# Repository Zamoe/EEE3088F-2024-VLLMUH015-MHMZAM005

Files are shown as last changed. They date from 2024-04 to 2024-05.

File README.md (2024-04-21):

# EEE3088F-2024-VLLMUH015-MHMZAM005 - Group 29
Git Repo for EEE3088F group 29 2024 at the University of Cape Town.

The project for EEE3088F aims to design subassemblies for a micromouse, namely the power and sensing subsystem. 
The GitHub repo contains the Kicad Project files for the final PCBs for the project.

The power system is done by Muhammed Vally - VLLMUH015
The sensing subsystem is done by Zameer Mahomed - MHMZAM005

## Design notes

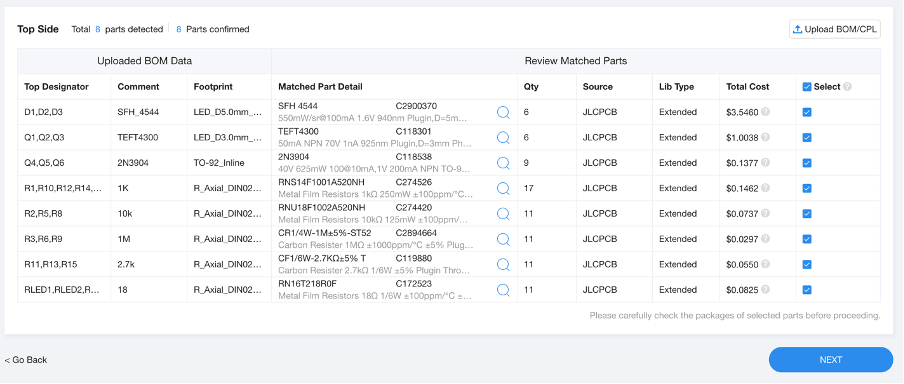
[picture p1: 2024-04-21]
EEE3088F_MHMZAM005_Sensing/jlcpcb/EEE3088F_Project_JLCPCBBOM_MHMZAM005.png

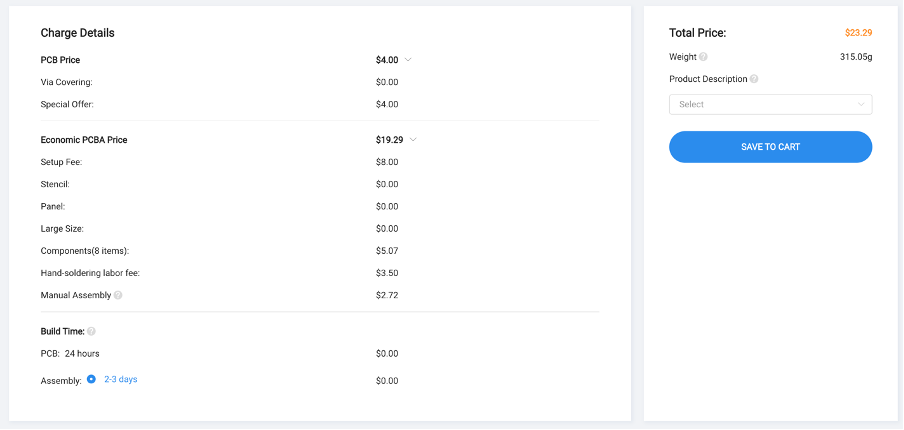
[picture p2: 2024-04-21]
EEE3088F_MHMZAM005_Sensing/jlcpcb/EEE3088F_Project_JLCPCBacceptance_MHMZAM005.png

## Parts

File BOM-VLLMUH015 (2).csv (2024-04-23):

Comment | Designator | Footprint | LCSC
0.1u | C6 | C_0805_2012Metric
10k | R2 | R_0805_2012Metric
0.1u | C5 | C_0805_2012Metric
0.1u | C3 | C_0805_2012Metric
Jumper_2_Open | JP5 | SolderJumper-2_P1.3mm_Bridged2Bar_Pad1.0x1.5mm
1.1k | R4 | R_0805_2012Metric
Jumper_2_Open | JP4 | SolderJumper-2_P1.3mm_Bridged2Bar_Pad1.0x1.5mm
2.2k | R3 | R_0805_2012Metric
10k | R1 | R_0805_2012Metric
Conn_02x01 | J2 | PinSocket_1x02_P2.54mm_Vertical
Jumper_2_Open | JP7 | SolderJumper-2_P1.3mm_Bridged2Bar_Pad1.0x1.5mm
Jumper_2_Open | JP2 | SolderJumper-2_P1.3mm_Bridged2Bar_Pad1.0x1.5mm
Jumper_2_Open | JP1 | SolderJumper-2_P1.3mm_Bridged2Bar_Pad1.0x1.5mm
0.1u | C4 | C_0805_2012Metric
Conn_02x08_Odd_Even | J1 | PinSocket_2x08_P2.54mm_Vertical
DRV8837 | U2 | WSON-8-1EP_2x2mm_P0.5mm_EP0.9x1.6mm
LED | D1 | LED_0805_2012Metric
Jumper_2_Open | JP6 | SolderJumper-2_P1.3mm_Bridged2Bar_Pad1.0x1.5mm
DRV8837 | U3 | WSON-8-1EP_2x2mm_P0.5mm_EP0.9x1.6mm
LED | D2 | LED_0805_2012Metric
10u | C8 | C_0805_2012Metric
0.4 | R6 | R_0805_2012Metric
Conn_01x02_Pin | J3 | PinHeader_1x02_P2.54mm_Vertical
TP4056 | U4 | ESOP8_UMW-L
10u | C7 | C_0805_2012Metric
1k | R7 | R_0805_2012Metric
1k | R8 | R_0805_2012Metric

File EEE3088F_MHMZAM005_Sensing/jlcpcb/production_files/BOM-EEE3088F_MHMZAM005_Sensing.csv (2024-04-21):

Comment | Designator | Footprint | LCSC
TEFT4300 | Q1,Q2,Q3 | LED_D3.0mm_Horizontal_O1.27mm_Z2.0mm | C118301
2N3904 | Q4,Q5,Q6 | TO-92_Inline | C118538
2.7k | R11,R13,R15 | R_Axial_DIN0207_L6.3mm_D2.5mm_P2.54mm_Vertical | C119880
18 | RLED1,RLED2,RLED3 | R_Axial_DIN0207_L6.3mm_D2.5mm_P2.54mm_Vertical | C172523
10k | R2,R5,R8 | R_Axial_DIN0207_L6.3mm_D2.5mm_P2.54mm_Vertical | C274420
1K | R1,R10,R12,R14,R4,R7 | R_Axial_DIN0207_L6.3mm_D2.5mm_P2.54mm_Vertical | C274526
1M | R3,R6,R9 | R_Axial_DIN0207_L6.3mm_D2.5mm_P2.54mm_Vertical | C2894664
SFH_4544 | D1,D2,D3 | LED_D5.0mm_Horizontal_O1.27mm_Z9.0mm | C2900370
Jumper_2_Open | JP4 | SolderJumper-2_P1.3mm_Open_Pad1.0x1.5mm
Jumper_2_Open | JP1 | SolderJumper-2_P1.3mm_Open_Pad1.0x1.5mm
Jumper_2_Open | JP15 | SolderJumper-2_P1.3mm_Open_Pad1.0x1.5mm
Jumper_2_Open | JP13 | SolderJumper-2_P1.3mm_Open_Pad1.0x1.5mm
Jumper_2_Open | JP2 | SolderJumper-2_P1.3mm_Open_Pad1.0x1.5mm
Jumper_2_Open | JP7 | SolderJumper-2_P1.3mm_Open_Pad1.0x1.5mm
Jumper_2_Open | JP5 | SolderJumper-2_P1.3mm_Open_Pad1.0x1.5mm
Jumper_2_Open | JP11 | SolderJumper-2_P1.3mm_Open_Pad1.0x1.5mm
Jumper_2_Open | JP9 | SolderJumper-2_P1.3mm_Open_Pad1.0x1.5mm
Jumper_2_Open | JP6 | SolderJumper-2_P1.3mm_Open_Pad1.0x1.5mm
Jumper_2_Open | JP10 | SolderJumper-2_P1.3mm_Open_Pad1.0x1.5mm
Jumper_2_Open | JP14 | SolderJumper-2_P1.3mm_Open_Pad1.0x1.5mm
Jumper_2_Open | JP3 | SolderJumper-2_P1.3mm_Open_Pad1.0x1.5mm
Jumper_2_Open | JP12 | SolderJumper-2_P1.3mm_Open_Pad1.0x1.5mm
Jumper_2_Open | JP8 | SolderJumper-2_P1.3mm_Open_Pad1.0x1.5mm
Conn_02x14_Odd_Even | J1 | PinHeader_2x14_P2.54mm_Vertical

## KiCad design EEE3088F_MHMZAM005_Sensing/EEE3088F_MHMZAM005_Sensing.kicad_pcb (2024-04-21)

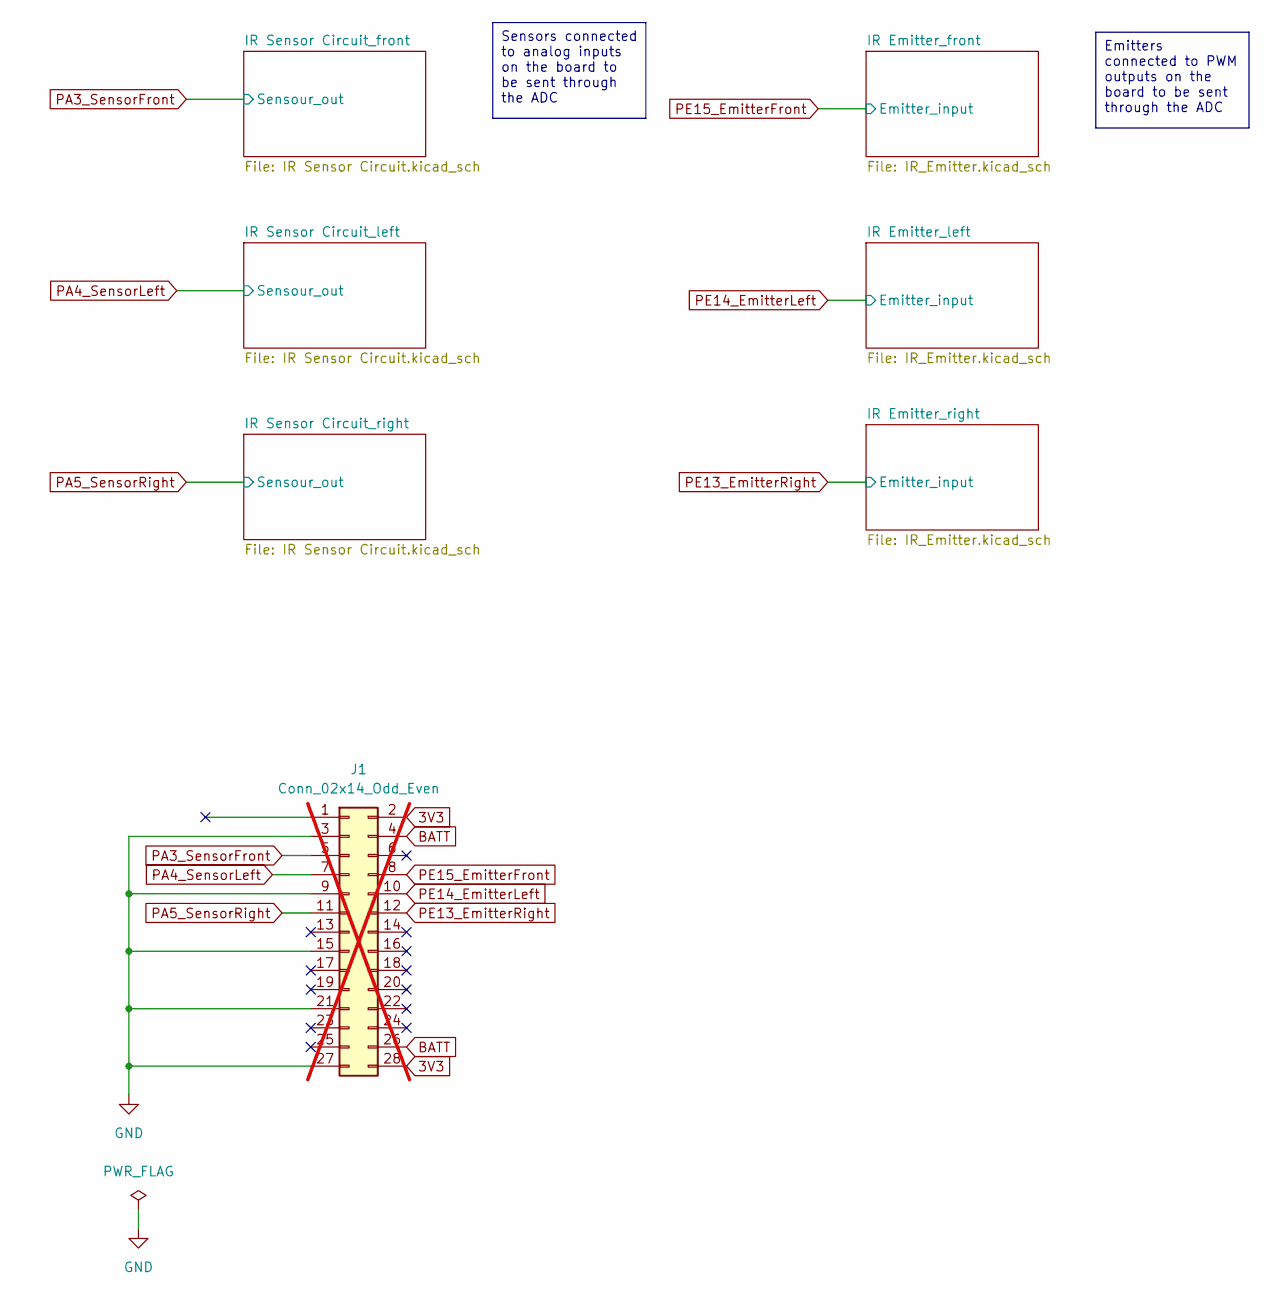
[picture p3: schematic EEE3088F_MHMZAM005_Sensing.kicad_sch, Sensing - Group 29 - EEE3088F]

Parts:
J1: Conn_02x14_Odd_Even; PinHeader_2x14_P2.54mm_Vertical; not fitted

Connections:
3V3: J1.2, J1.28; also elsewhere on the board
BATT: J1.4, J1.26
GND: J1.3, J1.9, J1.15, J1.21, J1.27; also elsewhere on the board
PA3: J1.5; also elsewhere on the board
PA4: J1.7; also elsewhere on the board
PA5: J1.11; also elsewhere on the board
PE13: J1.12; also elsewhere on the board
PE14: J1.10; also elsewhere on the board
PE15: J1.8; also elsewhere on the board

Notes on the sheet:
Sensors connected to analog inputs on the board to be sent through the ADC
Emitters connected to PWM outputs on the board to be sent through the ADC

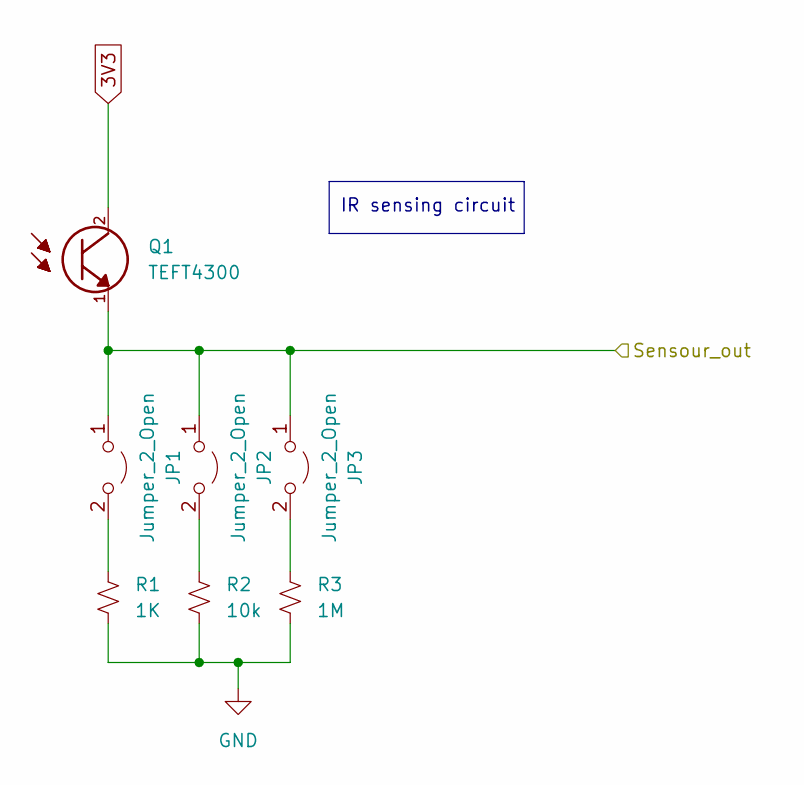
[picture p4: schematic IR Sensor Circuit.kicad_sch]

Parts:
JP1, JP2, JP3: Jumper_2_Open; SolderJumper-2_P1.3mm_Open_Pad1.0x1.5mm
Q1: TEFT4300; LED_D3.0mm_Horizontal_O1.27mm_Z2.0mm; LCSC C118301
R1: 1K; R_Axial_DIN0207_L6.3mm_D2.5mm_P2.54mm_Vertical; LCSC C274526
R2: 10k; R_Axial_DIN0207_L6.3mm_D2.5mm_P2.54mm_Vertical; LCSC C274420
R3: 1M; R_Axial_DIN0207_L6.3mm_D2.5mm_P2.54mm_Vertical; LCSC C2894664

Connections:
3V3: Q1.2; also elsewhere on the board
GND: R1.2, R2.2, R3.1; also elsewhere on the board
unnamed: JP1.2 (B), R1.1
unnamed: JP2.2 (B), R2.1
unnamed: JP3.2 (B), R3.2
PA3: JP1.1 (A), JP2.1 (A), JP3.1 (A), Q1.1; also elsewhere on the board

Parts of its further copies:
JP4, JP5, JP6, JP7, JP8, JP9: Jumper_2_Open; SolderJumper-2_P1.3mm_Open_Pad1.0x1.5mm
Q2, Q3: TEFT4300; LED_D3.0mm_Horizontal_O1.27mm_Z2.0mm; LCSC C118301
R4, R7: 1K; R_Axial_DIN0207_L6.3mm_D2.5mm_P2.54mm_Vertical; LCSC C274526
R5, R8: 10k; R_Axial_DIN0207_L6.3mm_D2.5mm_P2.54mm_Vertical; LCSC C274420
R6, R9: 1M; R_Axial_DIN0207_L6.3mm_D2.5mm_P2.54mm_Vertical; LCSC C2894664

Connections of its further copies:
3V3: Q2.2, Q3.2; also elsewhere on the board
GND: R4.2, R5.2, R6.1, R7.2, R8.2, R9.1; also elsewhere on the board
unnamed: JP4.2 (B), R4.1
unnamed: JP5.2 (B), R5.1
unnamed: JP6.2 (B), R6.2
unnamed: JP7.2 (B), R7.1
unnamed: JP8.2 (B), R8.1
unnamed: JP9.2 (B), R9.2
PA4: JP4.1 (A), JP5.1 (A), JP6.1 (A), Q2.1; also elsewhere on the board
PA5: JP7.1 (A), JP8.1 (A), JP9.1 (A), Q3.1; also elsewhere on the board

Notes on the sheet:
IR sensing circuit

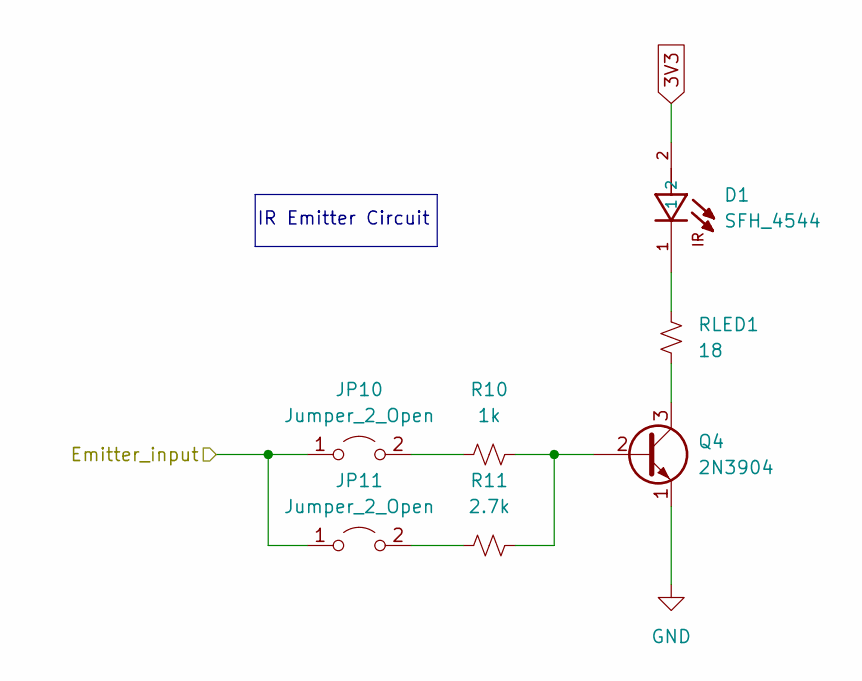
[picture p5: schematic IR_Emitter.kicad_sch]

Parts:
D1: SFH_4544; LED_D5.0mm_Horizontal_O1.27mm_Z9.0mm; PARTREV 1.3; LCSC C2900370
JP10, JP11: Jumper_2_Open; SolderJumper-2_P1.3mm_Open_Pad1.0x1.5mm
Q4: 2N3904; TO-92_Inline; LCSC C118538
R10: 1k; R_Axial_DIN0207_L6.3mm_D2.5mm_P2.54mm_Vertical; LCSC C274526
R11: 2.7k; R_Axial_DIN0207_L6.3mm_D2.5mm_P2.54mm_Vertical; LCSC C119880
RLED1: 18; R_Axial_DIN0207_L6.3mm_D2.5mm_P2.54mm_Vertical; LCSC C172523

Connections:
3V3: D1.2; also elsewhere on the board
GND: Q4.1 (E); also elsewhere on the board
unnamed: D1.1, RLED1.2
unnamed: JP10.2 (B), R10.2
unnamed: JP11.2 (B), R11.1
unnamed: Q4.2 (B), R10.1, R11.2
unnamed: Q4.3 (C), RLED1.1
PE15: JP10.1 (A), JP11.1 (A); also elsewhere on the board

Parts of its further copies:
D2, D3: SFH_4544; LED_D5.0mm_Horizontal_O1.27mm_Z9.0mm; PARTREV 1.3; LCSC C2900370
JP12, JP13, JP14, JP15: Jumper_2_Open; SolderJumper-2_P1.3mm_Open_Pad1.0x1.5mm
Q5, Q6: 2N3904; TO-92_Inline; LCSC C118538
R12, R14: 1k; R_Axial_DIN0207_L6.3mm_D2.5mm_P2.54mm_Vertical; LCSC C274526
R13, R15: 2.7k; R_Axial_DIN0207_L6.3mm_D2.5mm_P2.54mm_Vertical; LCSC C119880
RLED2, RLED3: 18; R_Axial_DIN0207_L6.3mm_D2.5mm_P2.54mm_Vertical; LCSC C172523

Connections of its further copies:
3V3: D2.2, D3.2; also elsewhere on the board
GND: Q5.1 (E), Q6.1 (E); also elsewhere on the board
unnamed: D2.1, RLED2.2
unnamed: D3.1, RLED3.2
unnamed: JP12.2 (B), R12.2
unnamed: JP13.2 (B), R13.1
unnamed: JP14.2 (B), R14.2
unnamed: JP15.2 (B), R15.1
unnamed: Q5.2 (B), R12.1, R13.2
unnamed: Q5.3 (C), RLED2.1
unnamed: Q6.2 (B), R14.1, R15.2
unnamed: Q6.3 (C), RLED3.1
PE13: JP14.1 (A), JP15.1 (A); also elsewhere on the board
PE14: JP12.1 (A), JP13.1 (A); also elsewhere on the board

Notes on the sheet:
IR Emitter Circuit

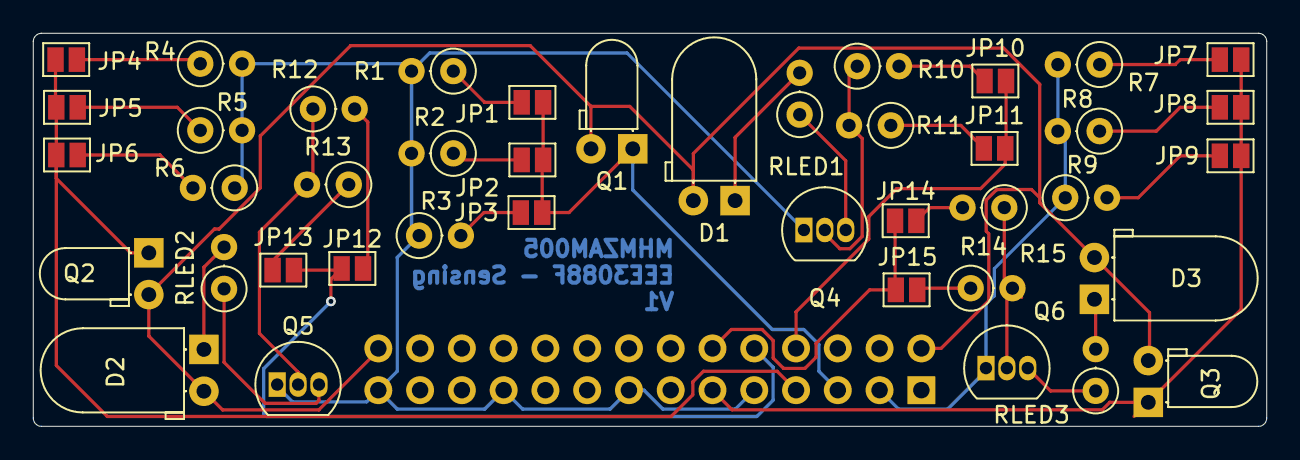
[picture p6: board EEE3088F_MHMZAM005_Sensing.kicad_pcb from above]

Board: 2 copper layers, 75.0 x 23.9 mm, 43 parts (1 on the bottom side), 33 nets.

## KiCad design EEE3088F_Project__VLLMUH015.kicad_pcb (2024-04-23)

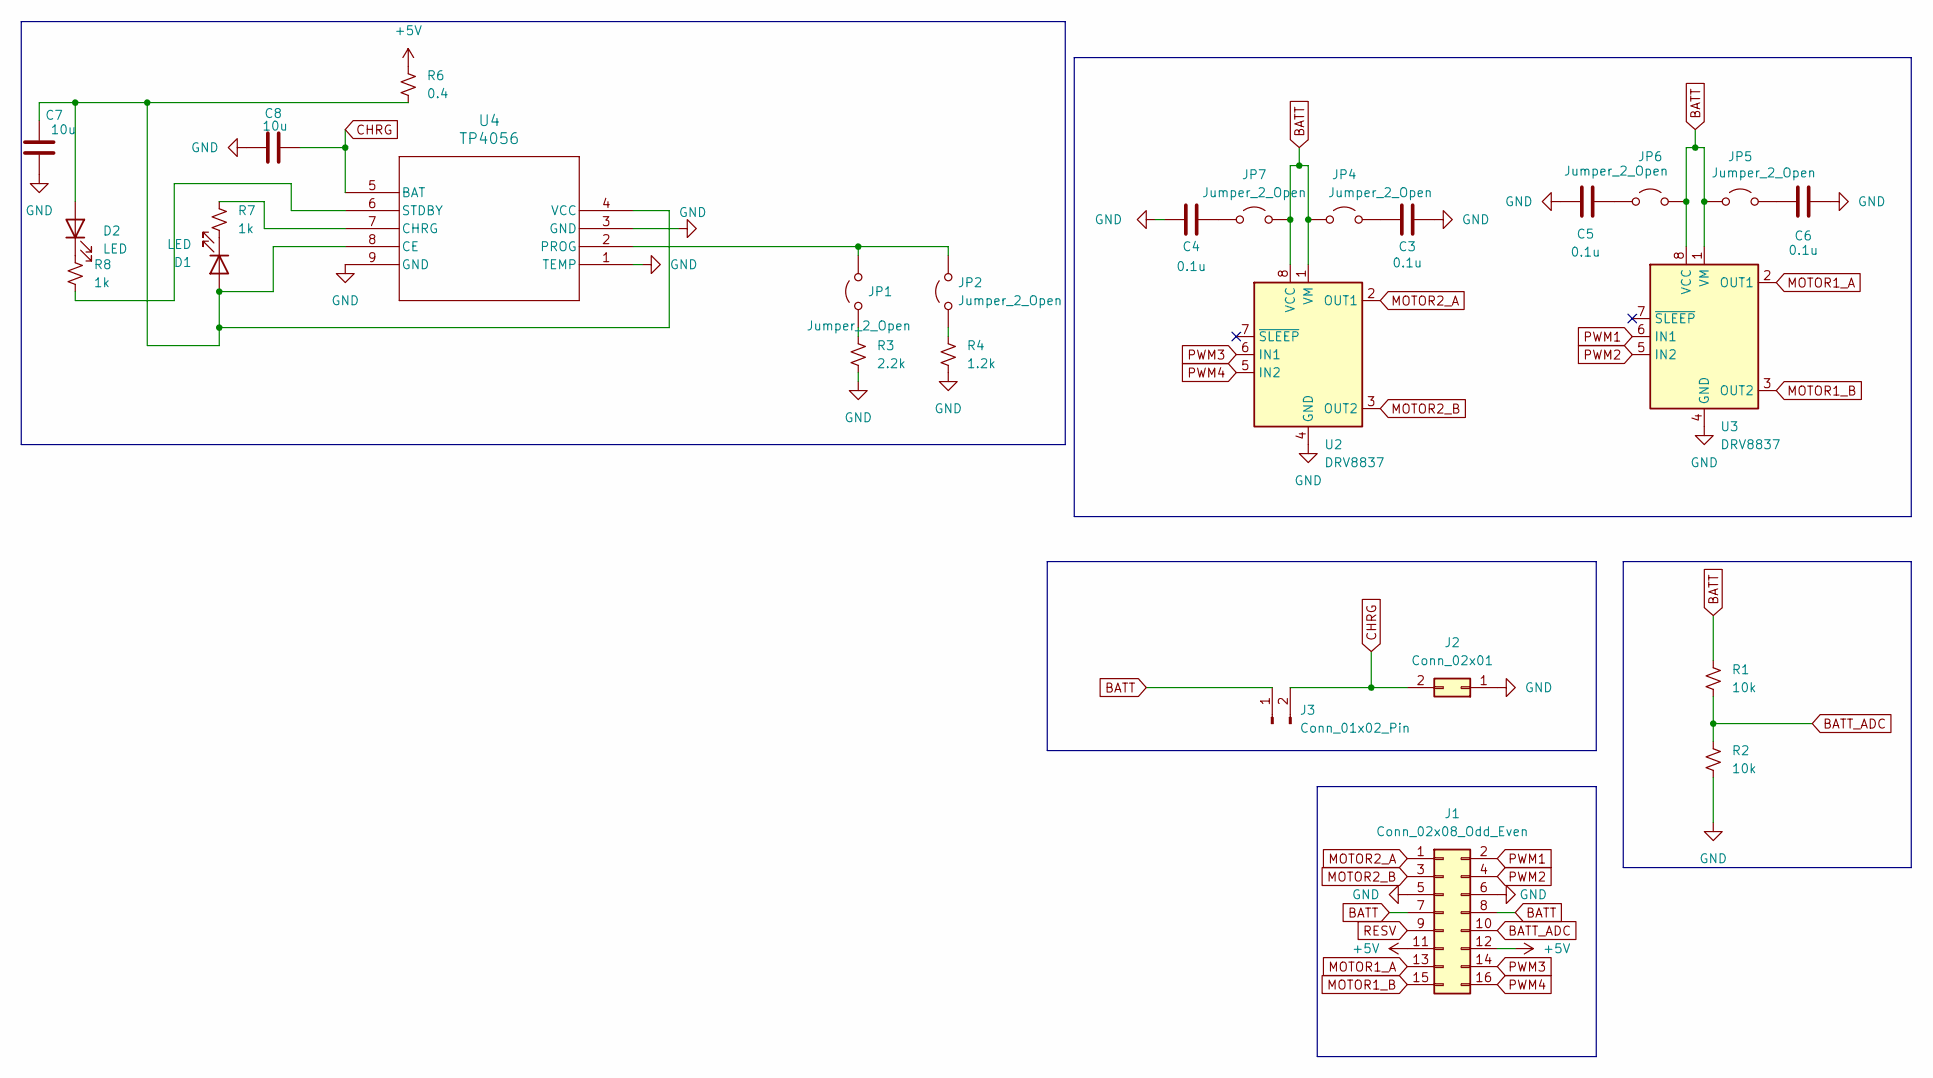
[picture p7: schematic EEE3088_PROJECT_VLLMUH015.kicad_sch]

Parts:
C3, C4, C5, C6: 0.1u; C_0805_2012Metric
C7, C8: 10u; C_0805_2012Metric
D1, D2: LED; LED_D1.8mm_W1.8mm_H2.4mm_Horizontal_O1.27mm_Z1.6mm
J1: Conn_02x08_Odd_Even; PinSocket_2x08_P2.54mm_Horizontal
J2: Conn_02x01; PinSocket_1x02_P2.54mm_Vertical
J3: Conn_01x02_Pin; PinHeader_1x02_P2.54mm_Vertical
JP1, JP2, JP4, JP5, JP6, JP7: Jumper_2_Open; SolderJumper-2_P1.3mm_Bridged2Bar_Pad1.0x1.5mm
R1, R2: 10k; R_0805_2012Metric
R3: 2.2k; R_0805_2012Metric
R4: 1.2k; R_0805_2012Metric
R6: 0.4; R_0805_2012Metric
R7, R8: 1k; R_0805_2012Metric
U2, U3: DRV8837; WSON-8-1EP_2x2mm_P0.5mm_EP0.9x1.6mm
U4: TP4056; ESOP8_UMW-L

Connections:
+5V: J1.11, J1.12, R6.1
BATT: J1.7, J1.8, J3.1, JP4.1 (A), JP5.1 (A), JP6.2 (B), JP7.2 (B), R1.1, U2.1 (VM), U2.8 (VCC), U3.1 (VM), U3.8 (VCC)
BATT_ADC: J1.10, R1.2, R2.1
CHRG: C8.2, J2.2, J3.2, U4.5 (BAT)
GND: C3.2, C4.1, C5.1, C6.2, C7.2, C8.1, J1.5, J1.6, J2.1, R2.2, R3.2, R4.2, U2.4 (GND), U2.9 (GND), U3.4 (GND), U3.9 (GND), U4.1 (TEMP), U4.3 (GND), U4.9 (GND)
MOTOR1_A: J1.13, U3.2 (OUT1)
MOTOR1_B: J1.15, U3.3 (OUT2)
MOTOR2_A: J1.1, U2.2 (OUT1)
MOTOR2_B: J1.3, U2.3 (OUT2)
unnamed: C7.1, D1.2 (A), D2.2 (A), R6.2, U4.4 (VCC), U4.8 (CE)
unnamed: D1.1 (K), R7.2
unnamed: D2.1 (K), R8.2
unnamed: JP1.1 (A), R3.1
unnamed: JP1.2 (B), JP2.2 (B), U4.2 (PROG)
unnamed: JP2.1 (A), R4.1
unnamed: C3.1, JP4.2 (B)
unnamed: C6.1, JP5.2 (B)
unnamed: C5.2, JP6.1 (A)
unnamed: C4.2, JP7.1 (A)
unnamed: R7.1, U4.7 (CHRG)
unnamed: R8.1, U4.6 (STDBY)
PWM1: J1.2, U3.6 (IN1)
PWM2: J1.4, U3.5 (IN2)
PWM3: J1.14, U2.6 (IN1)
PWM4: J1.16, U2.5 (IN2)
RESV: J1.9

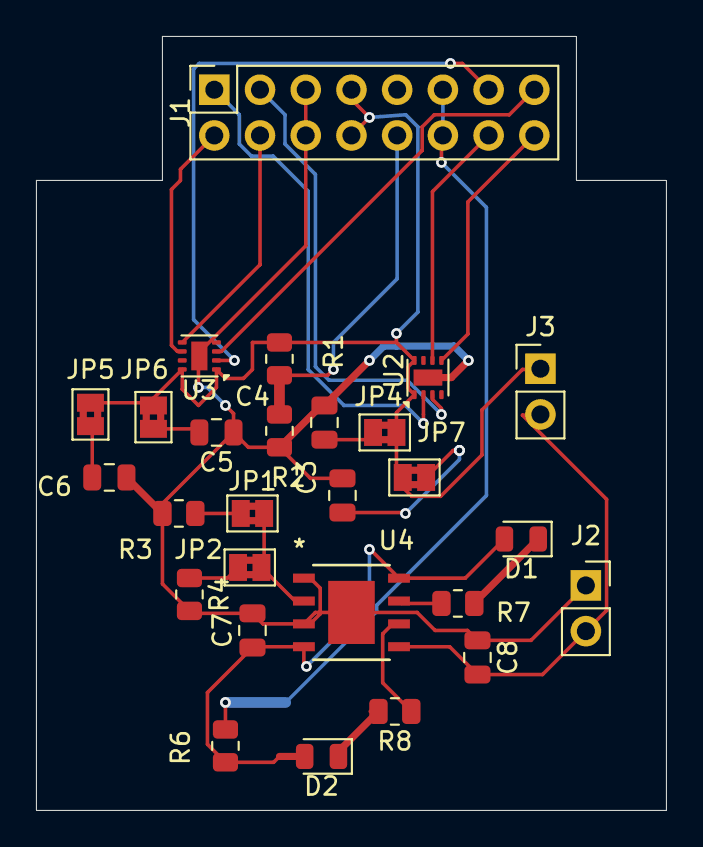
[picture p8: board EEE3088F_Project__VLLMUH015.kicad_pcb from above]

Board: 2 copper layers, 35.0 x 43.0 mm, 27 parts (0 on the bottom side), 25 nets.

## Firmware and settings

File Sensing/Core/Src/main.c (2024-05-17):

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
/* Includes ------------------------------------------------------------------*/
#include "main.h"

/* USER CODE BEGIN Includes */
#include "lcd_stm32f0.h"
#include "stdio.h"
/* USER CODE END Includes */

ADC_HandleTypeDef hadc;

TIM_HandleTypeDef htim1;

/* USER CODE BEGIN PV */
//ADC
uint32_t adc_valueFront =0;
uint32_t adc_valueLeft = 0;
uint32_t adc_valueRight = 0;

uint32_t threshold = 500;
uint32_t brightness;
uint32_t bright_percent = 100;

uint32_t temp_F;
uint32_t temp_L;
uint32_t temp_R;

char LCD_buffer[];

//for debouncing
unsigned long debounceTicks = 0; //time since last press
unsigned long debounceDuration = 20;    // time for debouncing; so far best results with 200
/* USER CODE END PV */

void SystemClock_Config(void);
static void MX_GPIO_Init(void);
static void MX_TIM1_Init(void);
static void MX_ADC_Init(void);
/* USER CODE BEGIN PFP */
void ADCPOLL_Front(void);
void ADCPOLL_Left(void);
void ADCPOLL_Right(void);
void LCD_switch(void);
void emitter_F(int);
void emitter_L(int);
void emitter_R(int);
void debounce_F(void);
void debounce_L(void);
void debounce_R(void);

void ADC1_COMP_IRQHandler(void);
/* USER CODE END PFP */

/**
  * @brief  The application entry point.
  * @retval int
  */
int main(void)
{

  /* MCU Configuration--------------------------------------------------------*/

  /* Reset of all peripherals, Initializes the Flash interface and the Systick. */
  HAL_Init();

  /* Configure the system clock */
  SystemClock_Config();

  /* Initialize all configured peripherals */
  MX_GPIO_Init();
  MX_TIM1_Init();
  MX_ADC_Init();
  /* USER CODE BEGIN 2 */
  //Initialise PWM
  HAL_TIM_PWM_Start(&htim1,TIM_CHANNEL_1);
  HAL_TIM_PWM_Start(&htim1,TIM_CHANNEL_2);
  HAL_TIM_PWM_Start(&htim1,TIM_CHANNEL_3);

  //LCD
  init_LCD();

  //PWM set brightness
  //set threshold
  //threshold = 0;
  //set emitter brightness from 0 to 47999
  brightness = (float)bright_percent/(float)100*(float)47999;
  //failsafe for if brightness gets set too bright
  if (brightness > 47999){
	  brightness = 47999;
  }
  /*//set PWM brightness
  	//pwm(brightness);
  	__HAL_TIM_SetCompare(&htim1, TIM_CHANNEL_1, brightness);
  	__HAL_TIM_SetCompare(&htim1, TIM_CHANNEL_2, brightness);
  	__HAL_TIM_SetCompare(&htim1, TIM_CHANNEL_3, brightness);
*/
  /* USER CODE END 2 */

  /* Infinite loop */
  /* USER CODE BEGIN WHILE */
  while (1)
  {
    /* USER CODE END WHILE */
	//lcd_command(CLEAR);
    /* USER CODE BEGIN 3 */

	//ADC code
	//change chsek5 to channel in use
	//ADCPOLL_Front();
	//ADCPOLL_Left();
	//ADCPOLL_Right();

	//HAL_GPIO_WritePin(GPIOB, LED7_Pin,SET);
	//HAL_GPIO_WritePin(GPIOB, LED6_Pin,SET);
	//HAL_GPIO_WritePin(GPIOB, LED5_Pin,SET);

	//code to control respective LEDS
	emitter_F(1);
	ADCPOLL_Front();
	if (adc_valueFront >= threshold){
		//debounce_F();
		HAL_GPIO_WritePin(GPIOB, LED6_Pin,SET);
		temp_F = temp_F -1;
	}
	else{
		temp_F = temp_F +1;
		if (temp_F >=3){
		HAL_GPIO_WritePin(GPIOB, LED6_Pin,RESET);
		temp_F=0;
		}
	}
	//HAL_Delay(200);
	//emitter_F(0);

	emitter_L(1);
	ADCPOLL_Left();
	if (adc_valueLeft >= threshold){
			//debounce_L();
			HAL_GPIO_WritePin(GPIOB, LED7_Pin,GPIO_PIN_SET);
			temp_L = temp_F -1;
		}
	else{
			temp_L = temp_L +1;
			if (temp_L >=3){
			HAL_GPIO_WritePin(GPIOB, LED7_Pin,RESET);
			temp_L=0;
			}
		}
	//HAL_Delay(200);
	//emitter_L(0);
	//temp =1;
	//while(temp == 1){
	emitter_R(1);
	ADCPOLL_Right();
	if (adc_valueRight >= threshold){
			//debounce_R();
			HAL_GPIO_WritePin(GPIOB, LED5_Pin,SET);
			temp_R = temp_F -1;
		}
	else{
			temp_R = temp_R +1;
			if (temp_R >=3){
			HAL_GPIO_WritePin(GPIOB, LED5_Pin,RESET);
			temp_R=0;
			}
		}
	//temp = 0;
	//}
	HAL_Delay(200);
	//emitter_R(0);


	//delay for no current
	//HAL_Delay(20);
	//HAL_GPIO_WritePin(LED6_GPIO_B, LED6_Pin,RESET);
	//HAL_GPIO_WritePin(LED5_GPIO_B, LED5_Pin,SET);

	//HAL_GPIO_TogglePin(GPIOB, LED7_Pin);

	//LCD printing comment out if polling too slow
	LCD_switch();

  }
  /* USER CODE END 3 */
}
//function to turn on emitter
void emitter_F(int input){
	if (input == 1 ){
		__HAL_TIM_SetCompare(&htim1, TIM_CHANNEL_1, brightness);
	}
	else {
		__HAL_TIM_SetCompare(&htim1, TIM_CHANNEL_1, 0);
	}
}
void emitter_L(int input){
	if (input == 1 ){
		__HAL_TIM_SetCompare(&htim1, TIM_CHANNEL_2, brightness);
	}
	else {
		__HAL_TIM_SetCompare(&htim1, TIM_CHANNEL_2, 0);
	}
}
void emitter_R(int input){
	if (input == 1 ){
		__HAL_TIM_SetCompare(&htim1, TIM_CHANNEL_3, brightness);
	}
	else {
		__HAL_TIM_SetCompare(&htim1, TIM_CHANNEL_3, 0);
	}
}
//function for LCD to remove if polling speed too low
void LCD_switch(void){
	lcd_command(CLEAR);
	sprintf(LCD_buffer, "F:%d", adc_valueFront); // Convert integer to string
	lcd_putstring(LCD_buffer);
	sprintf(LCD_buffer, " L:%d", adc_valueLeft); // Convert integer to string
	lcd_putstring(LCD_buffer);
	sprintf(LCD_buffer, " B:%d", bright_percent); // Convert integer to string
	lcd_putstring(LCD_buffer);
	lcd_command(LINE_TWO);
	sprintf(LCD_buffer, "R:%d", adc_valueRight); // Convert integer to string
	lcd_putstring(LCD_buffer);
	sprintf(LCD_buffer, " T:%d", threshold); // Convert integer to string
	lcd_putstring(LCD_buffer);
	HAL_Delay(250);
}
// function for adc
void ADCPOLL_Front(void){
	//ADC code
		//change chsek5 to channel in use
		ADC1 -> CHSELR = ADC_CHSELR_CHSEL0;
		HAL_ADC_Start(&hadc);
		HAL_Delay(10);
		while(HAL_ADC_PollForConversion(&hadc,HAL_MAX_DELAY)!= HAL_OK);
		HAL_ADC_Stop(&hadc);
		adc_valueFront = HAL_ADC_GetValue(&hadc);
		HAL_ADC_IRQHandler(&hadc); //Clear flags
}

void ADCPOLL_Left(void){
	//ADC code
		//change chsek5 to channel in use
		ADC1 -> CHSELR = ADC_CHSELR_CHSEL1;
		HAL_ADC_Start(&hadc);
		HAL_Delay(10);
		while(HAL_ADC_PollForConversion(&hadc,HAL_MAX_DELAY)!= HAL_OK);
		HAL_ADC_Stop(&hadc);
		adc_valueLeft = HAL_ADC_GetValue(&hadc);
		HAL_ADC_IRQHandler(&hadc); //Clear flags
}
void ADCPOLL_Right(void){
	//ADC code
		//change chsek5 to channel in use
		ADC1 -> CHSELR = ADC_CHSELR_CHSEL2;
		HAL_ADC_Start(&hadc);
		HAL_Delay(10);
		while(HAL_ADC_PollForConversion(&hadc,HAL_MAX_DELAY)!= HAL_OK);
		HAL_ADC_Stop(&hadc);
		adc_valueRight = HAL_ADC_GetValue(&hadc);
		HAL_ADC_IRQHandler(&hadc); //Clear flags
		//uint32_t val;  //poll ADC call ADC1_COMP_IRQHandler -> sets adc_val to adc val
		//HAL_ADC_Start(&hadc); //start ADC
		//HAL_ADC_PollForConversion(&hadc, 1); //poll at 1ms
		//adc_valueRight  = HAL_ADC_GetValue(&hadc); 	//get ADC value
		//return val;
}
void debounce_F(void)
{
	unsigned long currentTick = HAL_GetTick();
	// ensures that unwanted press noise within durationDuration are not regeistered
	if ((currentTick - debounceTicks) > debounceDuration){
		HAL_GPIO_WritePin(GPIOB, LED6_Pin,SET);

	}
	debounceTicks = currentTick; //set time since last tick

}

void debounce_L(void)
{
	unsigned long currentTick = HAL_GetTick();
	// ensures that unwanted press noise within durationDuration are not regeistered
	if ((currentTick - debounceTicks) > debounceDuration){
		HAL_GPIO_WritePin(GPIOB, LED7_Pin,SET);

	}
	debounceTicks = currentTick; //set time since last tick

}

void debounce_R(void)
{
	unsigned long currentTick = HAL_GetTick();
	// ensures that unwanted press noise within durationDuration are not regeistered
	if ((currentTick - debounceTicks) > debounceDuration){
		HAL_GPIO_WritePin(GPIOB, LED5_Pin,SET);

	}
	debounceTicks = currentTick; //set time since last tick

}

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


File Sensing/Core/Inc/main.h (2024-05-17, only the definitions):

#define LED5_Pin GPIO_PIN_5
#define LED5_GPIO_Port GPIOB
#define LED6_Pin GPIO_PIN_6
#define LED6_GPIO_Port GPIOB
#define LED7_Pin GPIO_PIN_7
#define LED7_GPIO_Port GPIOB

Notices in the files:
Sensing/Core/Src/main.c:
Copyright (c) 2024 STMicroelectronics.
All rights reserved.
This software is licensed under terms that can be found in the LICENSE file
